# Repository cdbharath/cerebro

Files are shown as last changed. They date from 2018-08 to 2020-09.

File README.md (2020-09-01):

## Cerebro 

A 4-DOF arm that can be controlled using Motor Imagery EEG signals and a haptic feed back system is implemented to materialize the exerted pressure.

The project proposes an approach towards EEG-driven position control of a robot arm by utilizing motor imagery, P300 waveform and Visually evoked Potential to align the robot arm with desired target position. The user produces motor imagery signals to control the motion of the arm. The P300 waveforms gives us sufficient data to detect whether we are performing any motion or even imagining doing so. This becomes even more accurate with C3, C4, PZ, FZ signals coming into picture. Taking these signals as features gives us appropriate information on the motion imagined by the user. This information can be used to control different parameters that are necessary for controlling the arm.

#### Progress:

##### Arm

1. Inverse kinematics equations
After doing a literature survey,the following paper was chosen for developing the inverse kinematics equation for the 4-DOF arm.
https://ieeexplore.ieee.org/document/7166008

2. Simulation in processing

A hand model was developed using Processing. The inverse kinematics equations were solved and the angle was fed to the model to validate the equations.

<p align="center">
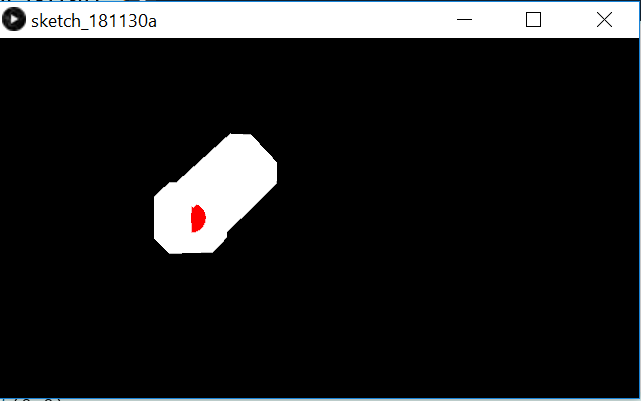
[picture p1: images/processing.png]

</p>

3. Simulation in Gazebo

The arm is simulated in gazebo and rviz by using the CADs designed by us as meshes. The actuation of the joints were controlled by changing the servo angles and the respective output is checked in the simulation.

<p align="center">
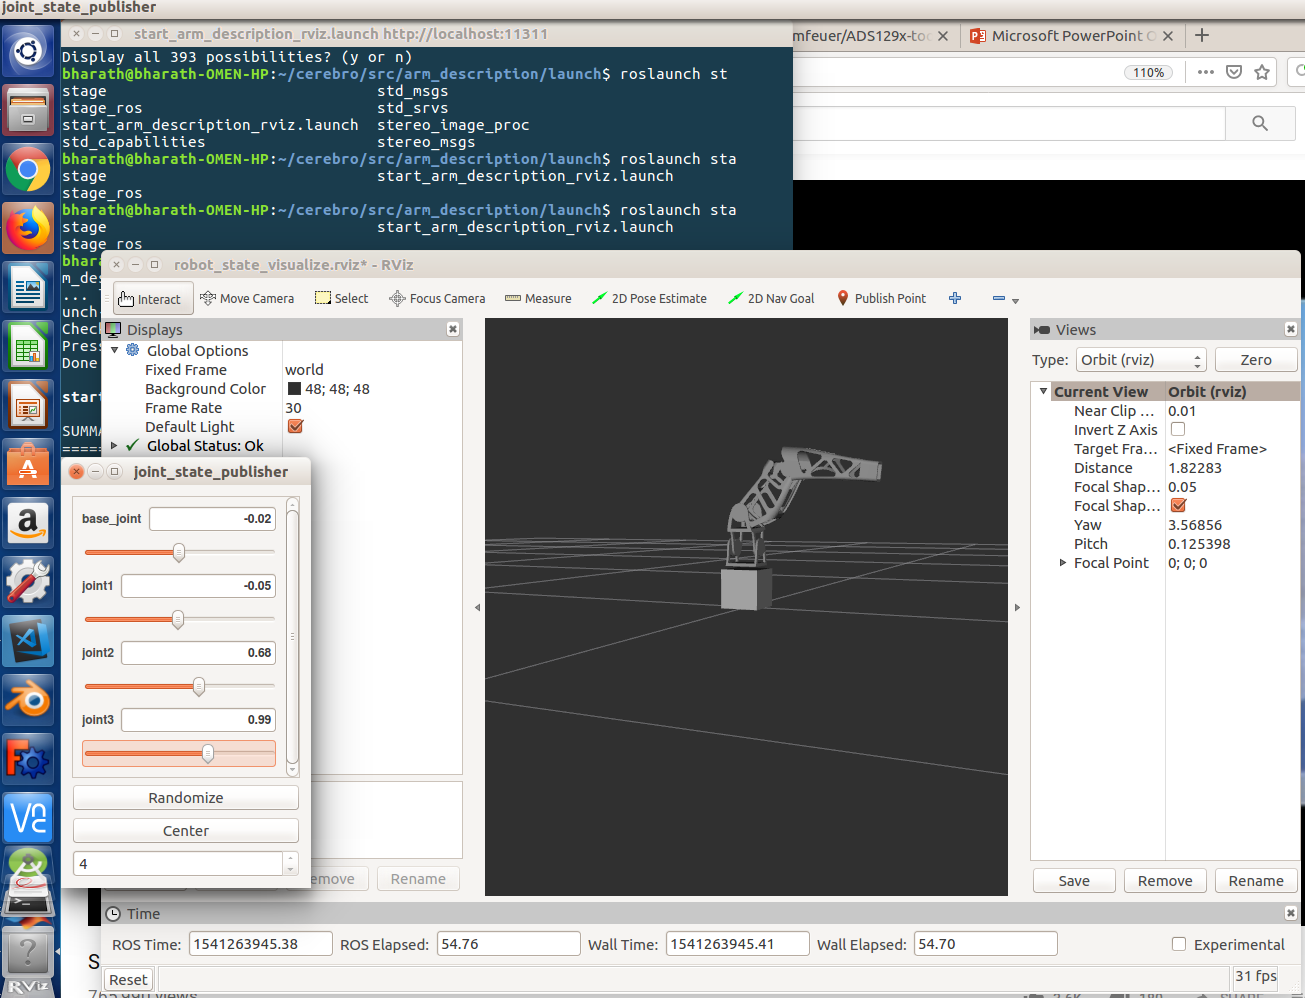
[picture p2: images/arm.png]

</p>

4. Assembly of hand with string mechanisms

The arm parts were assembled with two degrees of freedom in the base joint and one degree of freedom in the elbow joint with the hand attached to the end of the forearm link acting as an end effector. The CAD model of a hand, which had its finger controlled using the string mechanism was obtained from the InMoov website. This model was given for 3d printing. The 3d printed parts were assembled along with the strings. To facilitate the movement of the fingers of robotic arm, the string mechanism was researched upon and found suitable.  This mechanism uses the constancy of the length of wire passing through the finger structure to acquire the desired movement of finger. As the constancy of length was involved, we needed wires which are non stretchable over time and use. Hence we chose fishing braid as the wire that runs through the fingers of our robotic hand. This mechanism required 2 fishing braid wires to run through a single finger and the length of the wires and hence finger movements were controlled using servo motor rotation.

<p align="center">
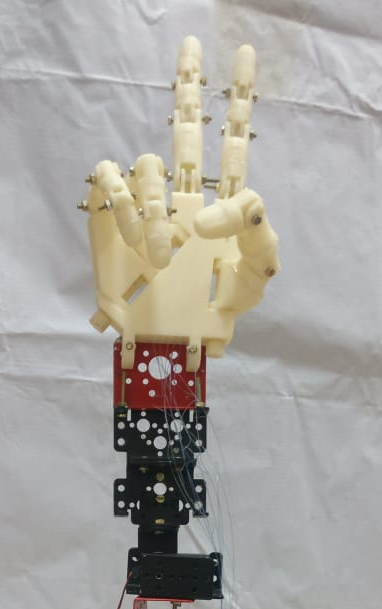
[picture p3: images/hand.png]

</p>

##### Signal Acquisition

1. Tina simulation of the circuit

Second order butterworth filter along with passive high pass filter was designed for the range of 5-20Hz for noise removal from the EEG. The output was then given to an instrumentation amplifier. This circuit was simulated in Tina before trying it out in Breadboard.

<p align="center">
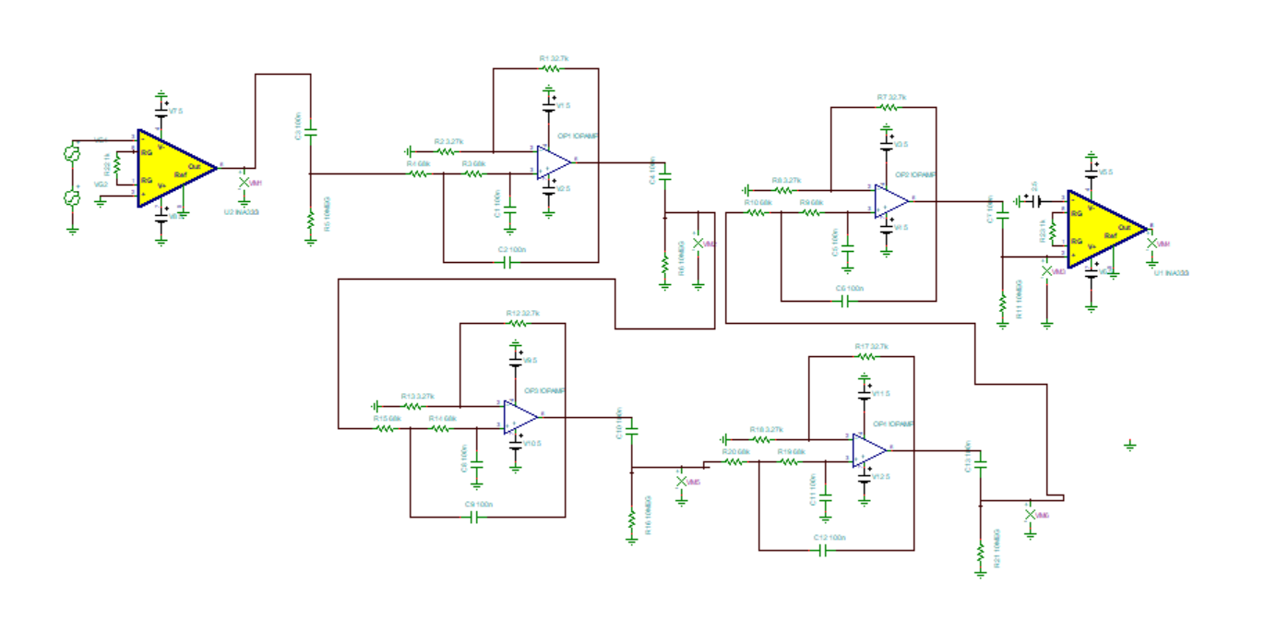
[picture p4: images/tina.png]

</p>

2. Breadboard implementation

The above circuit was practically implemented in the bread board and was validated.

3. PCB design

The same circuit was designed to make a PCB using Proteus software and printed for one channel.

<p align="center">
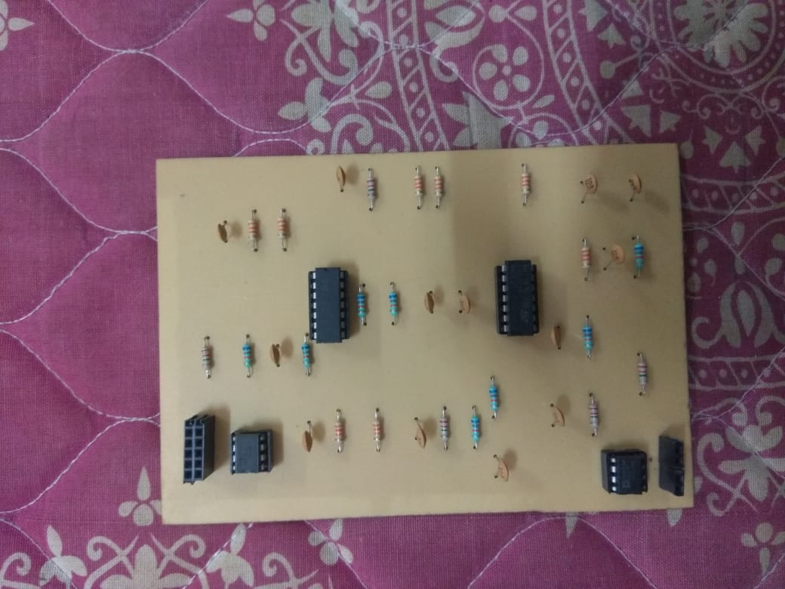
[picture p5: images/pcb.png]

</p>

4. EEG acquisition with OpenBCI Board	

As the designed board was for one channel, and for our application we need four channel, Open BCI board was used.
Due to the high impedance of the electrodes used and the absence of abrasion gel for reducing the impedance due to dead cells, Motor imagery signals were not obtained properly.
Hence EOG signals were acquired and the data was serially communicate to Arduino that checks with threshold and gives the appropriate output.Open BCI GUI was used to program the board on air.

<p align="center">
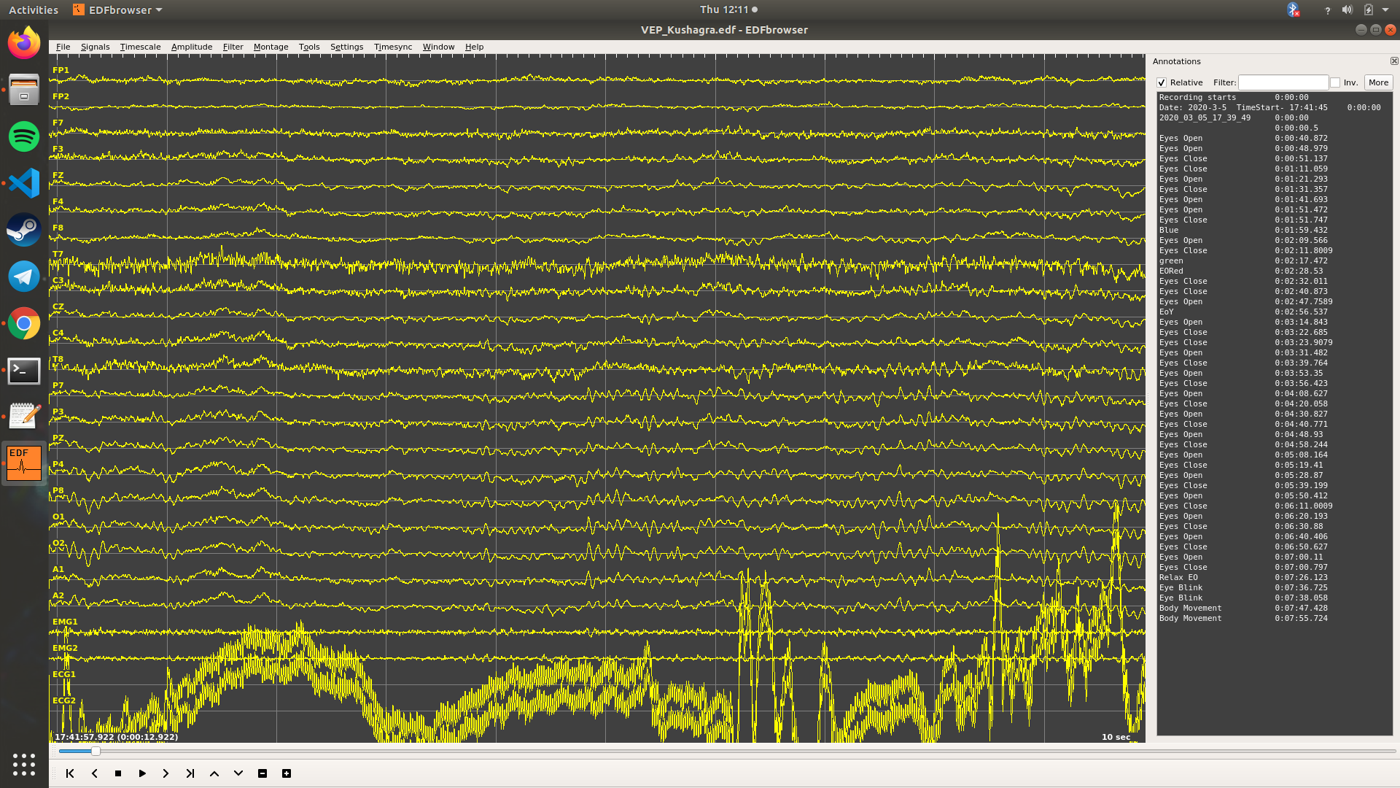
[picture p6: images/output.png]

</p>

##### Haptic feedback

1. Force sensors and Flex sensors
Ideated on interfacing force sensors and flex sensors on the robotic hand. Force sensors are used to measure the force experienced by the robotic arm and have necessary feedback through the pressure actuator in the user’s glove. Flex sensors are used to measure the movements of the finger and the position, which would be used as feedback signal for the positioning of finger. Force sensors and flex sensors were tested and their response to different forces and positioning were recorded.

2. Compressor

Compressor was tested with PWM to give out variable pressure that is necessary for filling the diaphragm. This will make sure that the required force is felt by the wearer of the glove, when the force sensors picks up the sensor values. 

3. Mould CAD design

The mould is a 1.8cm x 1cm x 0.4cm cuboid, designed in CAD and  3D printed. This is the Master mould which will be used for making the base of the balloon actuation mechanism that will will be attached to the fingers of the user.
        
4. Testing 1 (Mould)

One trial of making the PDMS mould was conducted. The curing agent an PDMS were added in the ratio of 1:10 and mixed using stirrer for 5 minutes after which the mixture was degassed in vacuum chamber. This mixture was then transferred to the mould and cured in hot air oven at 80 degrees for 6 hours.  The test did not yield the desired results, a s the PDMS had not solidified and instead had leaked outside the mould. The reason for it i that the terminal groups of the PDMS except hydroxyl and vinyl do not solidify, which I came to know later after analysing the reason for failure.

##### Signal Classification
 
1. CNN algorithm

A convolutional neural net is used to classify the signals     acquired from all the electrodes and classified for jaw clenching and blinking with decent accuracy.

2. Acquired Dataset

EOG data was acquired from electrodes placed on the forehead. Differential outputs from 4 electrodes were taken with respect to ground and used as features for training the model.

3. EOG signals

The EOG signals of 3 different people were obtained for different eye movements. The differences were clearly observable, though the range of values varied time to time and person to person. Therefore calibration and thresholding of the EOG signal was performed in python. The algorithm classifies the movement of eye to top/bottom/right/left.

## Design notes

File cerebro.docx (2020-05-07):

Work done:

Arm

  - Inverse kinematics equations

After doing a literature survey,the following paper was chosen for developing the inverse kinematics equation for the 4-DOF arm.

https://ieeexplore.ieee.org/document/7166008

  - Simulation in processing

A hand model was developed using Processing. The inverse kinematics equations were solved and the angle was fed to the model to validate the equations.


Link: https://github.com/bharath7kumar/Cerebro/blob/master/Hand_Model.pde

- Simulation

The arm is simulated in gazebo and rviz by using the CADs designed by us as meshes. The actuation of the joints were controlled by changing the servo angles and the respective output is checked in the simulation.

Link: https://github.com/bharath7kumar/Cerebro/tree/master/arm_description


  - Plywood arm assembly

An arm assembly using plywoods was tried by us. That didn’t prove to be efficient, and the metal gear servo motors couldn’t hold up the weight with its torque. This was tried to check the inverse kinematics equation.

  - Assembly using e-yantra arm

The arm parts were assembled with two degrees of freedom in the base joint and one degree of freedom in the elbow joint with the hand attached to the end of the forearm link acting as an end effector.

Finger Actuation

  - String mechanism ideation

To facilitate the movement of the fingers of robotic arm, the string mechanism was researched upon and found suitable. This mechanism uses the constancy of the length of wire passing through the finger structure to acquire the desired movement of finger. As the constancy of length was involved, we needed wires which are non stretchable over time and use. Hence we chose fishing braid as the wire that runs through the fingers of our robotic hand. This mechanism required 2 fishing braid wires to run through a single finger and the length of the wires and hence finger movements were controlled using servo motor rotation.

  - 3d printing of finger CADs

The CAD model of a hand, which had its finger controlled using the string mechanism was obtained from the InMoov website. This model was given for 3d printing.

  - Assembly of hand with string mechanisms

The 3d printed parts were assembled along with the strings. One servo motor for each finger was connected to control the actuation of the same. These servo motors were controlled using arduino uno and the desired finger actuation was observed.

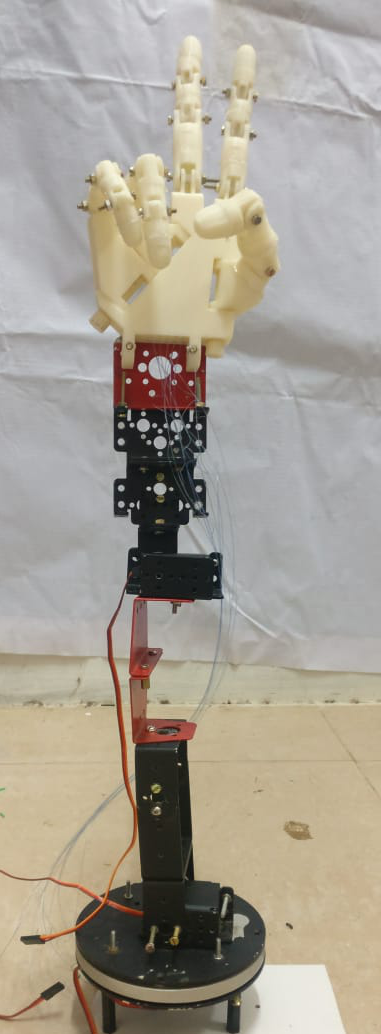
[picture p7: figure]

Signal Acquisition

  - Ads1299 Evaluation Board

Acquisition of signals using TI’s ADS1299 Evaluation board was tried. The SPI communication failed which may be due to the failure of board.Interface was first tried, using the ADS1299 GUI which the TI provided specially for this Evaluation board.

Secondly, Interface was done using SPI communication between the Arduino and the Evaluation board.

Hardware components used along with the board were checked to conclude that the board is at fault.

  - Tina simulation of the circuit

Second order butterworth filter along with passive high pass filter was designed for the range of 5-20Hz for noise removal from the EEG. The output was then given to an instrumentation amplifier. This circuit was simulated in Tina before trying it out in Breadboard.


  - Breadboard implementation

The above circuit was practically implemented in the bread board and was validated.

  - PCB design

The same circuit was designed to make a PCB using Proteus software and printed for one channel.


  - OpenBCI board

As the designed board was for one channel, and for our application we need four channel, Open BCI board was used.

Due to the high impedance of the electrodes used and the absence of abrasion gel for reducing the impedance due to dead cells, Motor imagery signals were not obtained properly.

Hence EOG signals were acquired and the data was serially communicate to Arduino that checks with threshold and gives the appropriate output.Open BCI GUI was used to program the board on air.

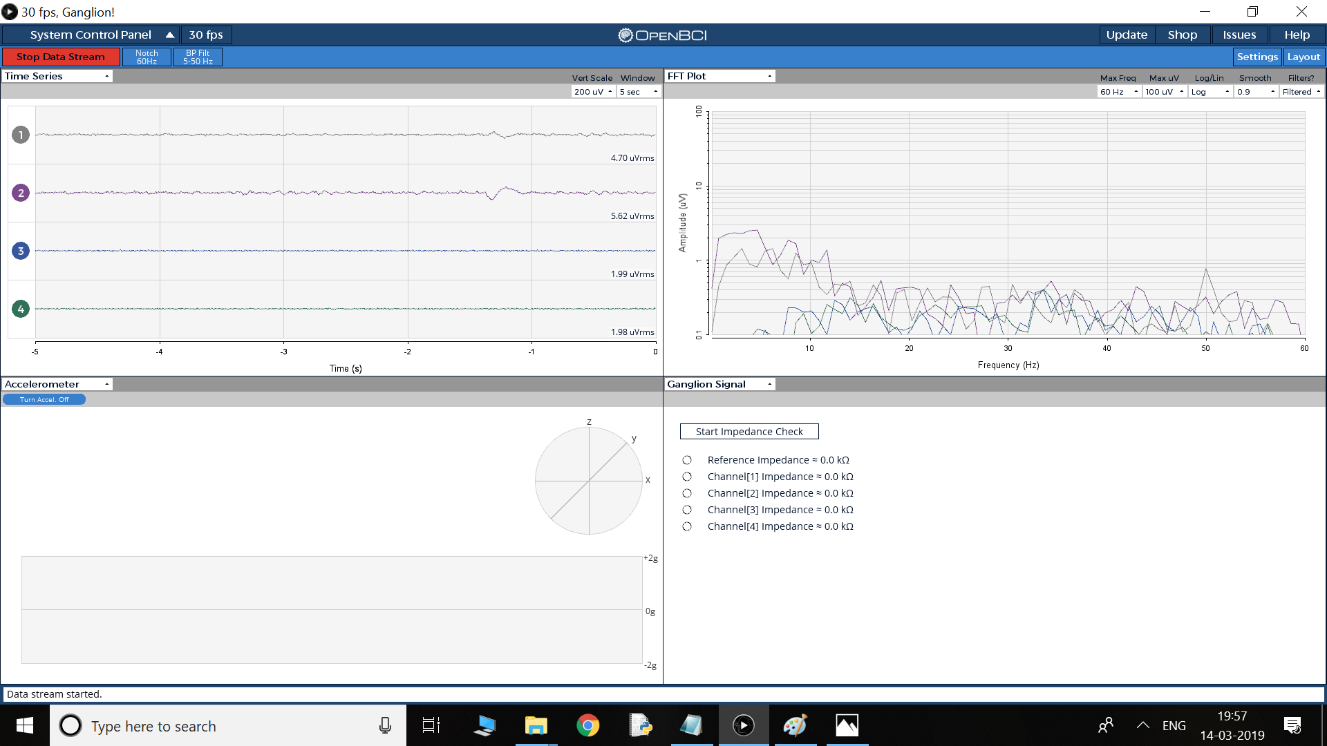
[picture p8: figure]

Haptic feedback

  - Force sensors and Flex sensors

Ideated on interfacing force sensors and flex sensors on the robotic hand. Force sensors are used to measure the force experienced by the robotic arm and have necessary feedback through the pressure actuator in the user’s glove. Flex sensors are used to measure the movements of the finger and the position, which would be used as feedback signal for the positioning of finger. Force sensors and flex sensors were tested and their response to different forces and positioning were recorded.

  - Compressor

Compressor was tested with PWM to give out variable pressure that is necessary for filling the diaphragm. This will make sure that the required force is felt by the wearer of the glove, when the force sensors picks up the sensor values.

  - Mould CAD design

The mould is a 1.8cm x 1cm x 0.4cm cuboid, designed in CAD

and 3D printed. This is the Master mould which will be used

for making the base of the balloon actuation mechanism that will

will be attached to the fingers of the user.

  - Testing 1 (Mould)

One trial of making the PDMS mould was conducted. The curing agent an PDMS were added in the ratio of 1:10 and mixed using stirrer for 5 minutes after which the mixture was degassed in vacuum chamber. This mixture was then transferred to the mould and cured in hot air oven at 80 degrees for 6 hours. The test did not yield the desired results, a s the PDMS had not solidified and instead had leaked outside the mould. The reason for it i that the terminal groups of the PDMS except hydroxyl and vinyl do not solidify, which I came to know later after analysing the reason for failure.

Signal Classification

  - CNN algorithm

A convolutional neural net is used to classify the signals acquired from all the electrodes and classified for jaw clenching and blinking with decent accuracy.

  - Acquired Dataset

EOG data was acquired from electrodes placed on the forehead. Differential outputs from 4 electrodes were taken with respect to ground and used as features for training the model.

Link: https://github.com/bharath7kumar/Cerebro/tree/master/data

  - EOG signals

The EOG signals of 3 different people were obtained for different eye movements. The differences were clearly observable, though the range of values varied time to time and person to person. Therefore calibration and thresholding of the EOG signal was performed in python. The algorithm classifies the movement of eye to top/bottom/right/left.

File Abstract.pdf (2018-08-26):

# Cerebro

Motor Imagery based Prosthetic arm control with Haptic feedback

Bharath, Amritha, Aradhana, Bhavya, Rakesh, Pooja, Veejay

Abstract

A 6-DOF arm that can be controlled using Motor Imagery EEG signals and a haptic feed back system is implemented to materialize the exerted pressure.

## 1 Introduction

The project proposes an approach towards EEG-driven position control of a robot arm by utilizing motor imagery, P300 waveform and Visually evoked Potential to align the robot arm with desired target position.
The user produces motor imagery signals to control the motion of the arm. The P300 waveforms gives us sufficient data to detect whether we are performing any motion or even imagining doing so. This becomes even more accurate with C3, C4, PZ, FZ signals coming into picture. Taking these signals as features gives us appropriate information on the motion imagined by the user. This information can be used to control different parameters that are necessary for controlling the arm.
This Project has a lot of Applications. This will facilitate the living of individuals with upper extremity impairment. The Brain-computer interface can act as a medium for them to use robotic arm for the activities of their daily life. Haptic feedback will give them the sense of touch. This can be achieved by giving neuro-feed back to the brain. The haptic feedback can be very helpful when it comes to invasive surgery using robotic arms.

## 2 Methodology

### 2.1 Building a 6DOF arm

A 6DOF humanoid arm is built by 3d printing the CAD model open sourced by Poppy Project, a humanoid robotic startup. The final arm will be capable of traversing any x,y,z coordinates within the range, along with rolling, rotating of the arm. Six servos are attached on the elbow, wrist and shoulder, each two respectively. Extra servos will be needed for the finger movements. The movement of the arm is achieved with inverse kinematics.

1

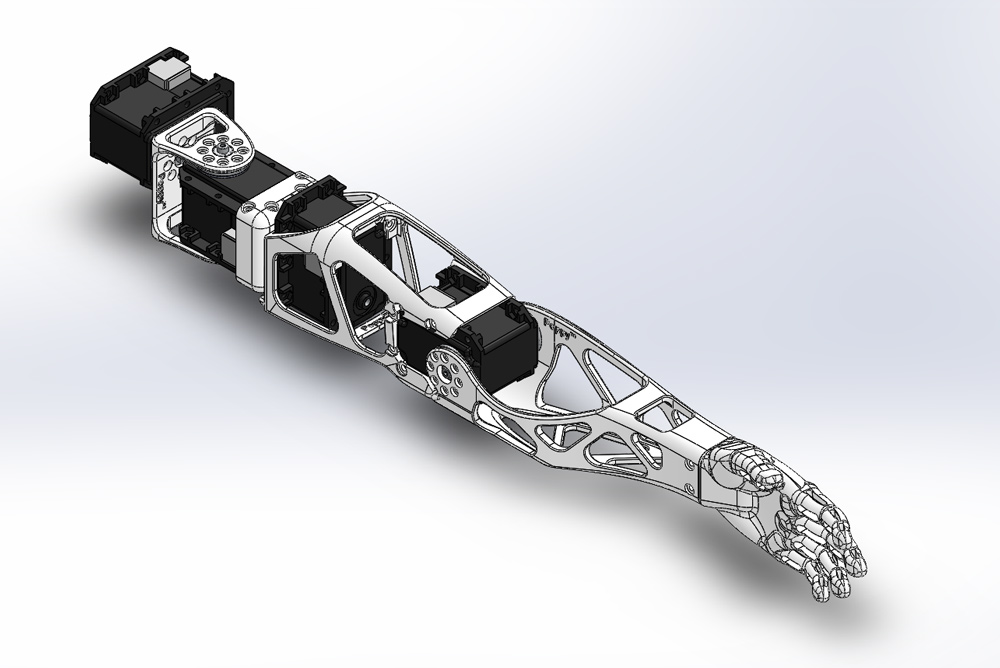
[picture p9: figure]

Figure 1: The CAD model.

### 2.2 Inverse Kinematics

Inverse kinematics problem of a robot is finding the angles of the robot by having the end position. It allows us to traverse our gripper to specific coordinate mentioned and grab a particular object. Higher degrees of freedom will have a more complicated solution. The length of each edge is considered to get the final joint angles.

### 2.3 Control with Flex sensors

The flex sensor uses flexible conductive ink printed on flexible base forming a resistor. It works when bent with the ink on the outside of the curve. When bent, the outside layer is stretched and thus extends, resulting in reduced cross section. This reduced cross section and increased length results in an increased resistance, which can be measured.
This variable resistance of the flex sensor can be mapped to different positions of the finger. Different fingers of the robotic arm will have different flex sensors attached to it. The position of each finger, calculated from the EEG Signal, will be the required value. The flex sensors’ resistance will give us actual positions of the fingers. A suitable linear control algorithm will be framed to bring the actual position close to or exactly same as the calculated position using servo motors.
The resistance of the flex sensor can be obtained by combining the flex sensor with a static resistor to create a voltage divider, which can produce a variable voltage that can be read by analog-to-digital converter of a micro controller.

### 2.4 Haptic feedback

Force sensors are placed at the fingers of the robotic arm. The data is serially transmitted to the controller.Glove has PDMS membrane embedded in it. PDMS is viscoelastic material.Balloon actuation is achieved by the pressure dependent swelling and saturation phenomena of 2 flexible PDMS diaphragms.Top

2

diaphragm layer has horizontal channels where the air can be pumped from an external compressor which is controlled using PWM in accordance with the data obtained from force sensor.

### 2.5 Electrode Placements

The signals we will be needing for motor imagery are C3, C4, PZ, FZ region. These regions are present in the central region of our head. EEG electrodes are placed in the respective positions along with the reference electrode which is placed over any of the ear lobe. The reference electrode is given as The reference electrode is given to shorted negative terminals of the channels, while the other four electrodes are given to positive terminal of the respective channels.

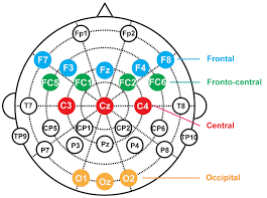
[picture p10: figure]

Figure 2: Electrode placement.

### 2.6 EEG signal Acquisition

ADS1299 is a device by Texas Instruments. It has 8 channels, that is, 8 differential amplifiers. The negative terminal of the amplifiers can be shorted and reference voltage is applied, which will be the same across all negative terminals. The common mode noise is significantly reduced on giving input signals through the differential amplifier. The dc noise is reduced by adding a High pass filter with sufficient cutoff voltage. The 50hz live-line voltage interference can be reduced in a similar way by adding a low pass filter with a cutoff frequency of 40hz. A better way to reduce 50hz noise is to implement second order butter worth filter ,the roll off doubles up reducing the noise even more.
The output signal from ADS1299 is sent to Arduino using serial Peripheral interface.This is further transferred to PC serially. Python receives the serial data and feeds the data to classification algorithm.

3

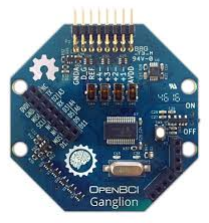
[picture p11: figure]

Figure 3: The acquisition board.

### 2.7 Motor Imagery Data Classification

The data is saved in a data buffer of length 5 seconds. The number of samples will be the baudrate * 5. This data is fed either to SVM Classifier or CNN or RNN. The model is chosen based on the validation accuracy. SVM is currently the popular algorithm used for EEG signal classification. The classic, one vs rest classification can be used to classify the signals from one another. But using Recurrent Neural Networks may improve the accuracy significantly since EEG signal is a time series. The data is fed into Recurrent neural networks with applicable hyper parameters to get the final output.

### 2.8 Control using Classification output

We have to control the up/down, right/left, top/bottom, yaw, pitch, roll of the arm. Since the only varying parameters in the inverse kinematics equation of 6dof arm are X, Y, Z coordinates, roll, pitch, yaw, we can easily control the arm using few parameters. An additional parameter is needed for the grasping of fists. The output from the classification algorithm can be used to control these parameters thereby controlling the arm. The two step process includes moving the arm in the horizontal plane right above the target object. The moving the arm vertically down until we reach the object. Then we use the grasp parameter to grab the object and again use the two step process to place the object somewhere else. The two step process is preferred because it requires comparatively lesser parameters and is easier to control.

## 3 Further Improvements

The Arm control can be further improved with visual feedback. The video camera may be placed in back of the hand or we can use the aerial view. Then

4

we can use the error in visual feed back for better control. Reinforcement learning algorithm can be used to train the arm from its mistakes. The model will allow the arm to overcome its previous mistakes, finally ending up doing the required action.

## 4 Requirements

### 4.1 Hardware Requirements

1. Acquisition device
2. 3d Printed STLs
3. EEG electrodes
4. Electrode paste
5. Servo Motors
6. Flex sensors
7. Air Pump
8. Rubber Gloves
9. Vibration sensors

### 4.2 Software Requirements

1. Python
2. ROS
3. Tensorflow or Pytorch
4. Arduino IDE

## 5 References

- Saugat Bhattacharyya, Amit KonarD, N. Tibarewala ”Motor imagery, P300 and error-related EEG-based robot arm movement control for rehabilitation purpose”
- Ming-ai , Meng Zhang , Yan-jun Sun ”A novel motor imagery EEG recognition method based on deep learning”
- Alireza Khatamian ”Solving Kinematics Problems of a 6-DOF Robot Manipulator”
- Poppy Project github repository ”https://github.com/poppy-project/Poppybasic-arms”

5

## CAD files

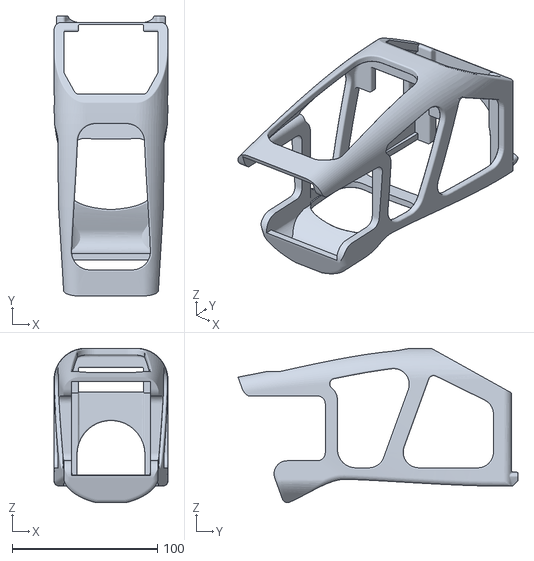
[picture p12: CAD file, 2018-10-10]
CADs/Arm/upper_arm.stl
78.5 x 192.9 x 106.3

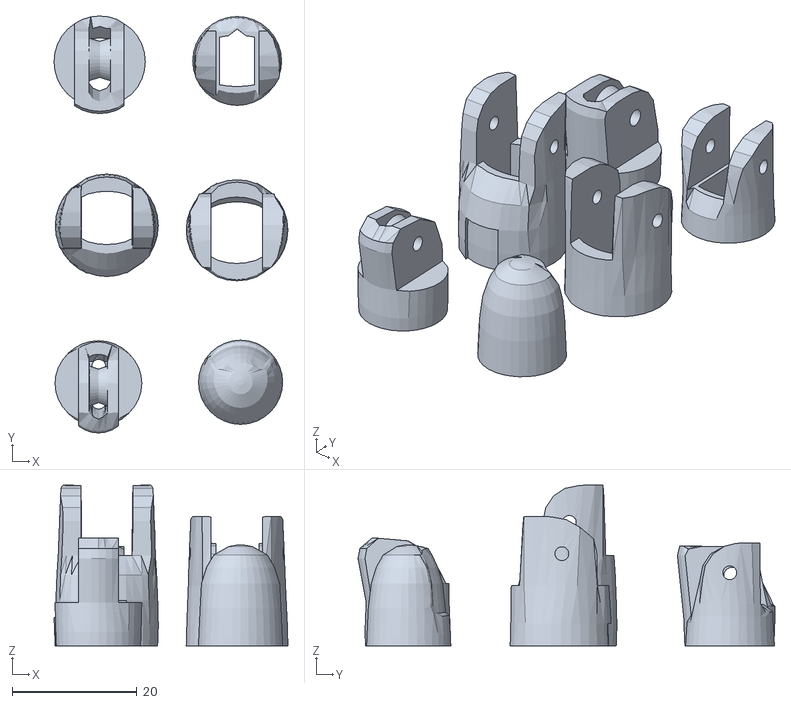
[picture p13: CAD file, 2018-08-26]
CADs/Hand/ringfinger3.stl
37.6 x 67.0 x 25.8

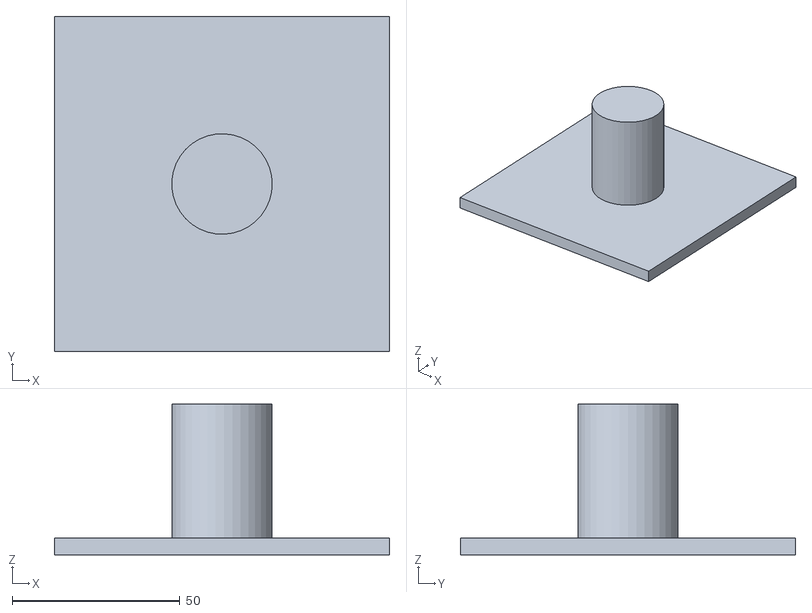
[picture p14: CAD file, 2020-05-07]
Simulation/New_arm/Sample CAD model/arm-cerebro-ross - shoulder-plate-1.STL
100.0 x 100.0 x 45.0

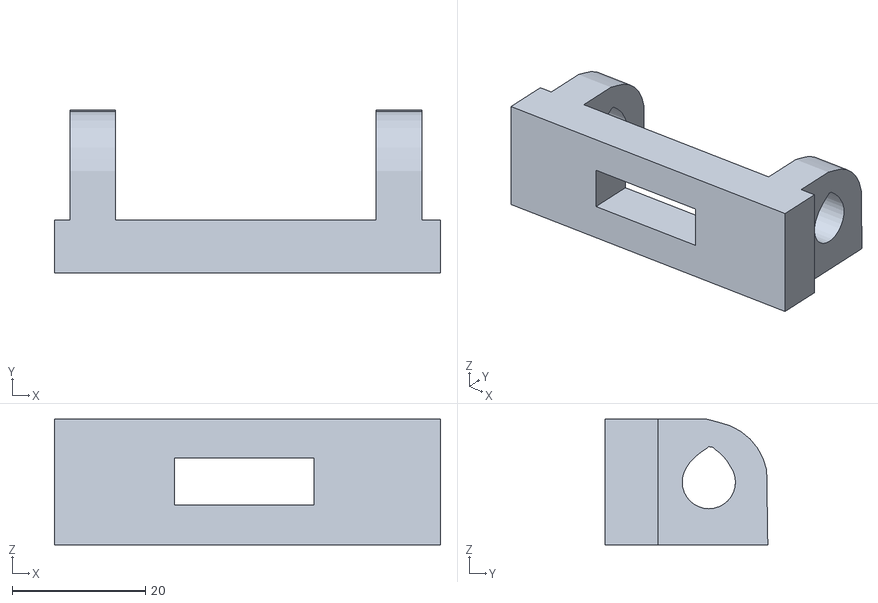
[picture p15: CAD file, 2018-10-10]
CADs/Arm/hand_connector.STL
58.0 x 24.4 x 18.9

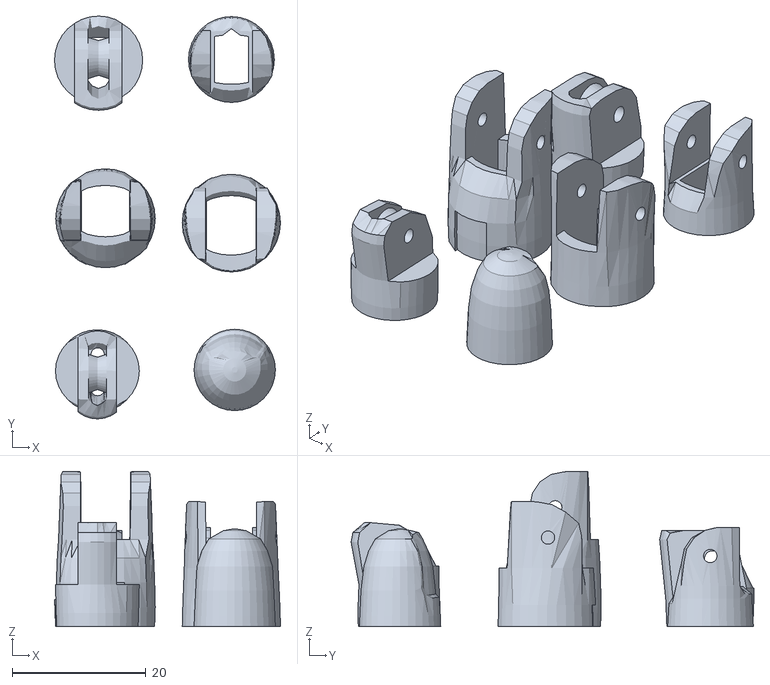
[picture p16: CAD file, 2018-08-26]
CADs/Hand/Auriculaire3.stl
33.8 x 60.3 x 23.2

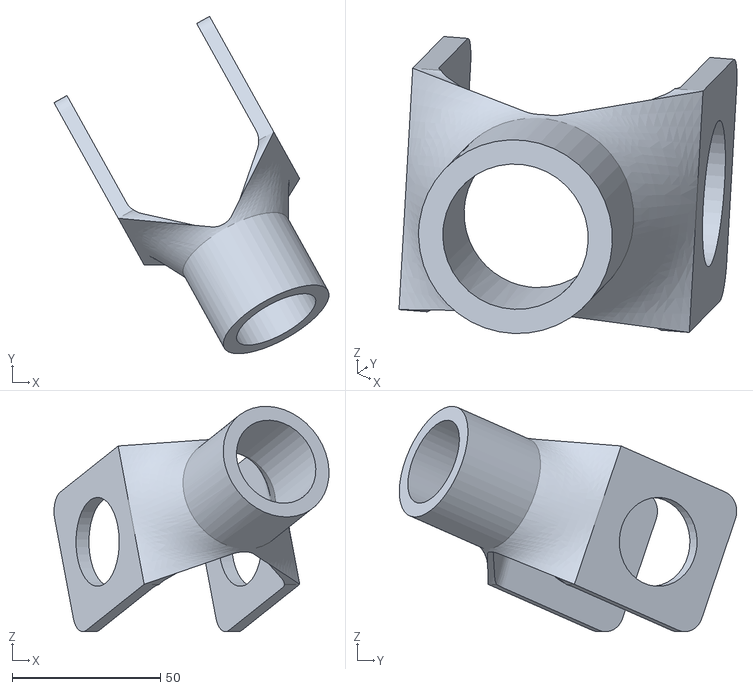
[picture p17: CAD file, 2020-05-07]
Simulation/New_arm/Sample CAD model/arm-cerebro-ross - shoulder-hinge-2.STL
92.7 x 113.8 x 75.9

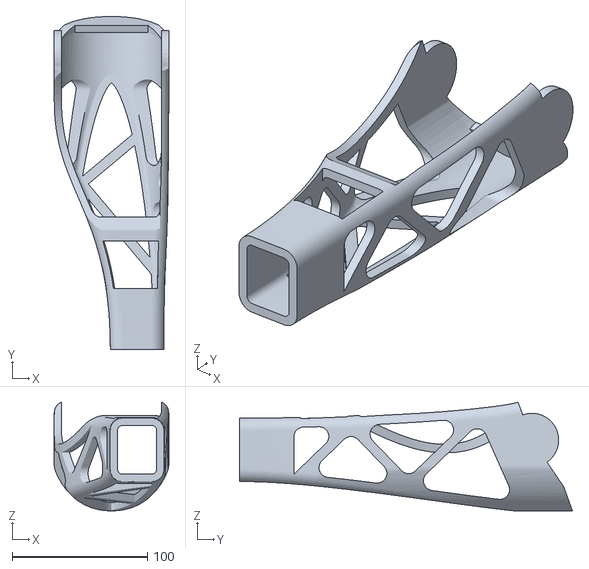
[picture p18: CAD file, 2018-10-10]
CADs/Arm/forearm.STL
84.6 x 246.0 x 80.4

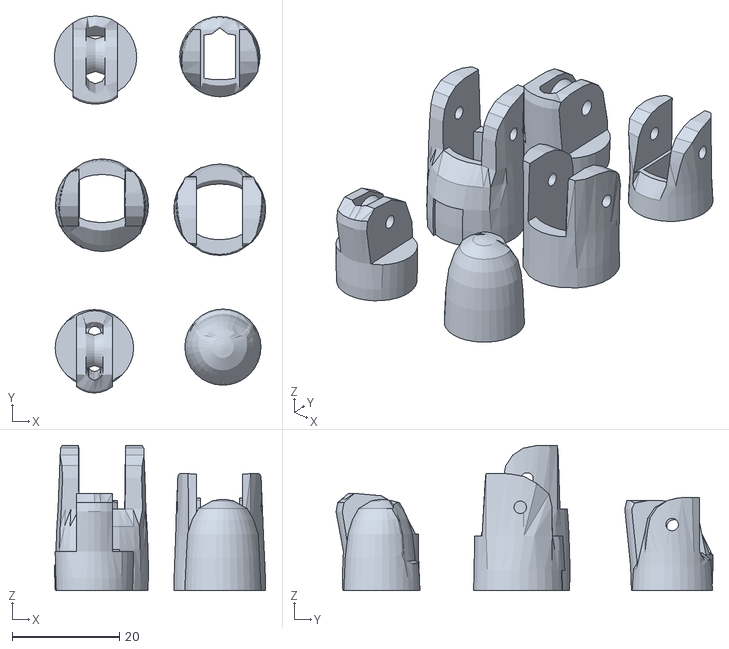
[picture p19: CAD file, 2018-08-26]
CADs/Hand/Index3.stl
39.4 x 70.2 x 27.0

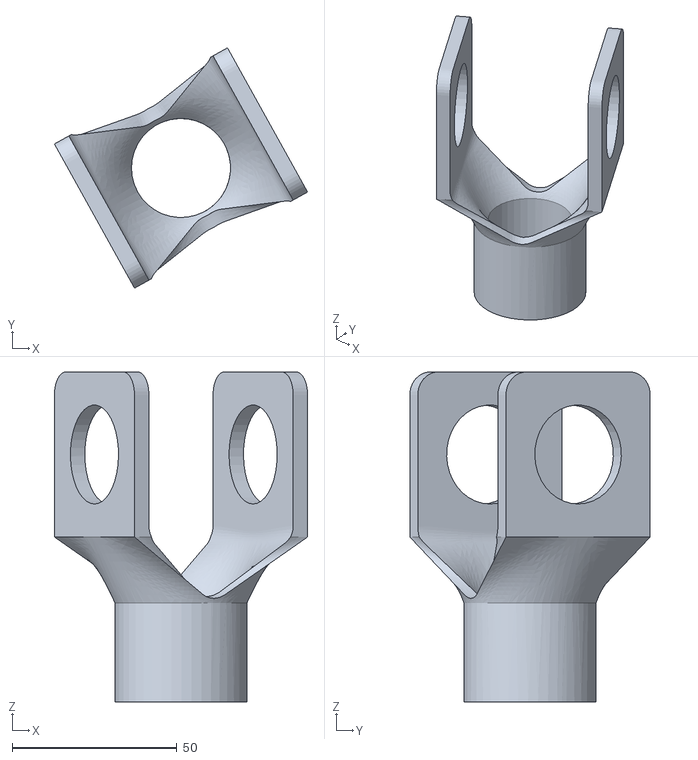
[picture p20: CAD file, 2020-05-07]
Simulation/New_arm/Sample CAD model/arm-cerebro-ross - shoulder-hinge-1.STL
76.7 x 72.8 x 100.0

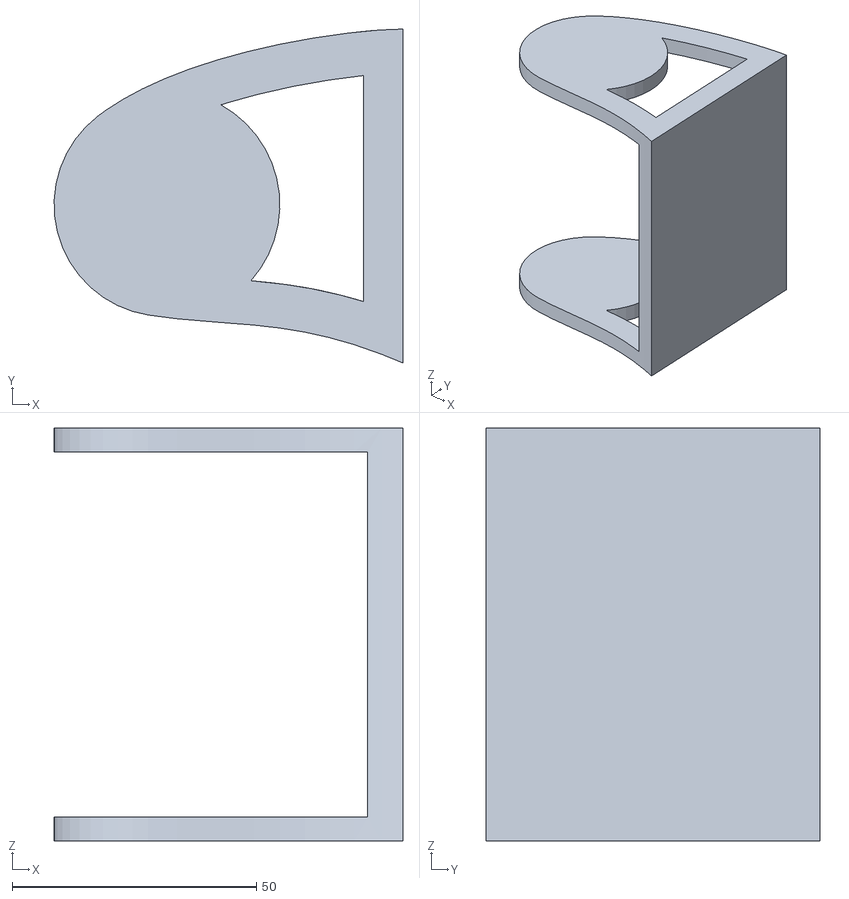
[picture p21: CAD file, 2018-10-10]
CADs/Arm/shoulder_connector_1.STL
71.4 x 68.4 x 84.6

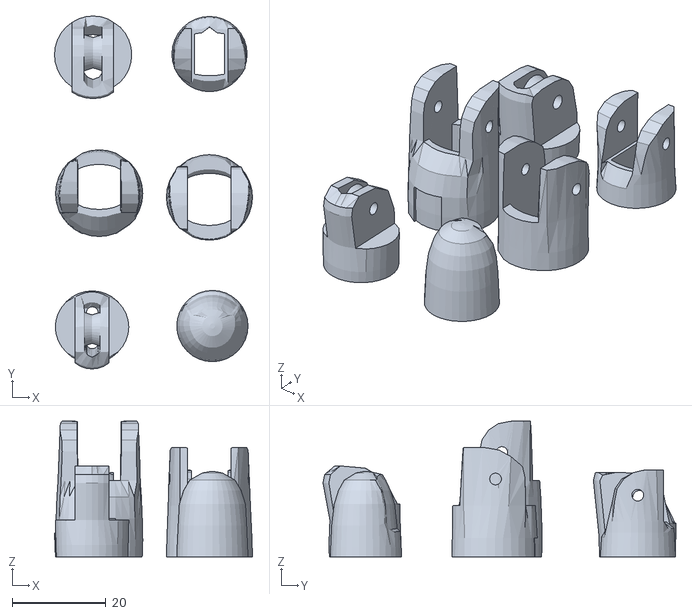
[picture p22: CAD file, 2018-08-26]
CADs/Hand/Majeure3.stl
42.2 x 75.2 x 29.0

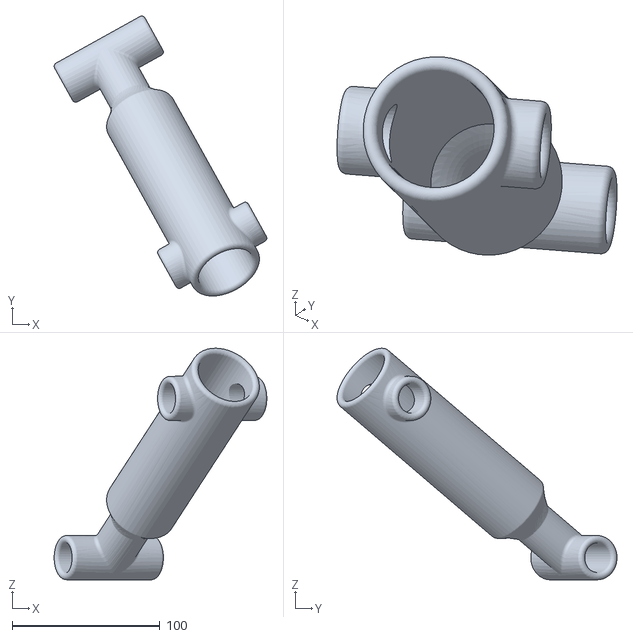
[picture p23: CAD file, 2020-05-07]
Simulation/New_arm/Sample CAD model/arm-cerebro-ross - arm-1.STL
143.9 x 189.5 x 156.8

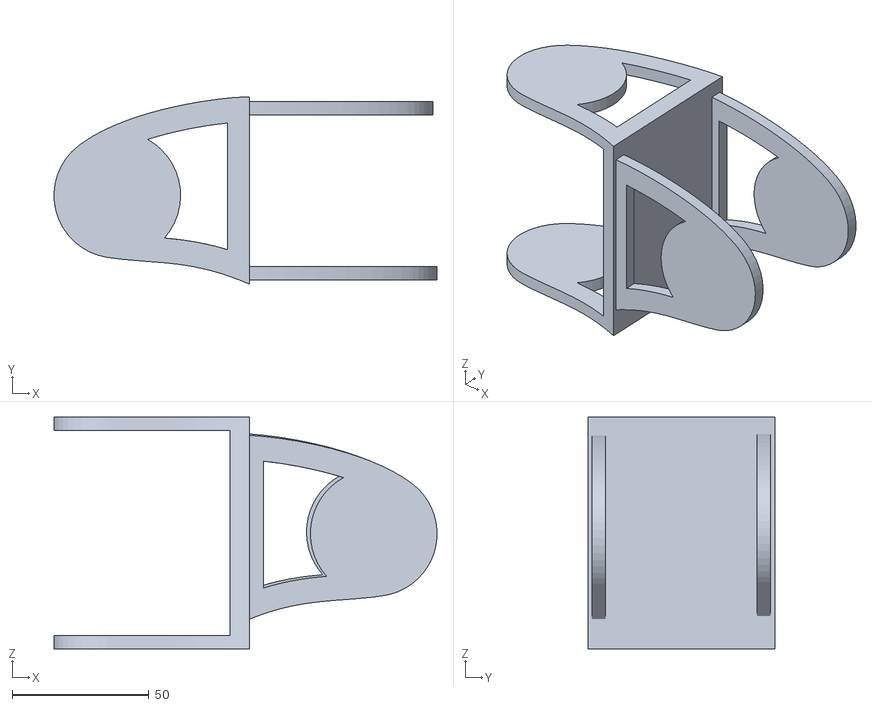
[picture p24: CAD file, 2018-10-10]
CADs/Arm/shoulder_connector_2.STL
139.8 x 68.4 x 84.6

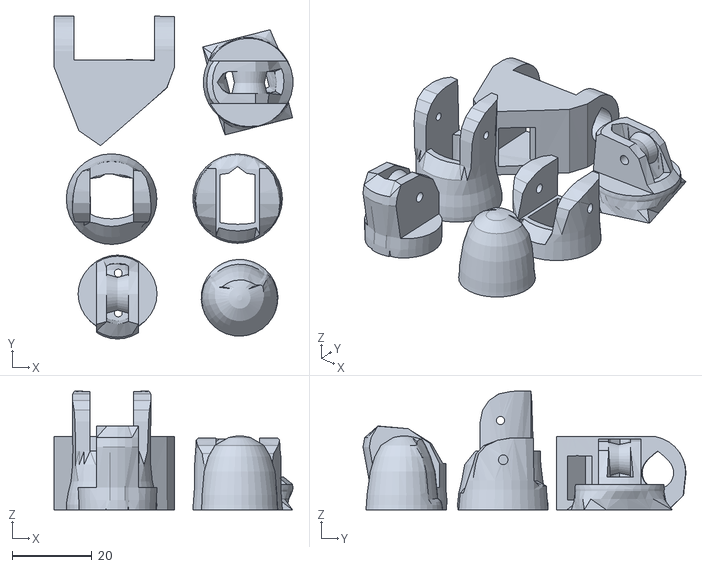
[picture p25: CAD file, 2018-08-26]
CADs/Hand/thumb5.stl
60.1 x 81.2 x 29.8

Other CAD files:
CADs/Hand/WristlargeV4.stl
CADs/Hand/WristsmallV4.stl
CADs/Hand/Bolt_entretoise7.stl

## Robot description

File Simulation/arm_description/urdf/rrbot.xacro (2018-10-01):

<?xml version="1.0"?>
<!-- Revolute-Revolute Manipulator -->
<robot name="rrbot" xmlns:xacro="http://www.ros.org/wiki/xacro">

  <!-- Constants for robot dimensions -->
  <xacro:property name="PI" value="3.1415926535897931"/>
  <xacro:property name="mass" value="1" /> <!-- arbitrary value for mass -->
  <xacro:property name="width" value="0.1" /> <!-- Square dimensions (widthxwidth) of beams -->
  <xacro:property name="height1" value="2" /> <!-- Link 1 -->
  <xacro:property name="height2" value="1" /> <!-- Link 2 -->
  <xacro:property name="height3" value="1" /> <!-- Link 3 -->
  <xacro:property name="camera_link" value="0.05" /> <!-- Size of square 'camera' box -->
  <xacro:property name="axel_offset" value="0.05" /> <!-- Space btw top of beam and the each joint -->

  <!-- Import all Gazebo-customization elements, including Gazebo colors -->
  <xacro:include filename="$(find rrbot_description)/urdf/rrbot.gazebo" />
  <!-- Import Rviz colors -->
  <xacro:include filename="$(find rrbot_description)/urdf/materials.xacro" />

  <!-- Used for fixing robot to Gazebo 'base_link' -->
  <link name="world"/>

  <joint name="fixed" type="fixed">
    <parent link="world"/>
    <child link="base"/>
  </joint>

  <!-- base -->
  <link name="base">
    <collision>
      <origin xyz="0 0 0.05" rpy="0 0 0"/>
      <geometry>
	<box size="0.1 0.1 0.1"/>
      </geometry>
    </collision>

    <visual>
      <origin xyz="0 0 0.05" rpy="0 0 0"/>
      <geometry>
	<box size="0.1 0.1 0.1"/>
      </geometry>
      <material name="orange"/>
    </visual>

    <inertial>
      <origin xyz="0 0 0" rpy="0 0 0"/>
      <mass value="${mass}"/>
      <inertia ixx="${mass / 12.0 * (width*width + height1*height1)}" ixy="0.0" ixz="0.0" iyy="${mass / 12.0 * (height1*height1 + width*width)}" iyz="0.0" izz="${mass / 12.0 * (width*width + width*width)}"/>
    </inertial>
  </link>

  <joint name="base_joint" type="continuous">
    <parent link="base"/>
    <child link="link1"/>
    <origin xyz="0 0 0" rpy="0 0 0"/>
    <axis xyz="0 0 1"/>
    <dynamics damping="0.7"/>
  </joint>

  <!-- link1 -->
  <link name="link1">
    <collision>
      <origin xyz="-0.039 0.042 0.18" rpy="1.57 1.57 0"/>
      <geometry>
	<mesh filename="package://arm_description/meshes/collision/shoulderconnector1.dae" scale="0.001 0.001 0.001"/>
      </geometry>
    </collision>

    <visual>
      <origin xyz="-0.039 0.042 0.18" rpy="1.57 1.57 0"/>
      <geometry>
	<mesh filename="package://arm_description/meshes/visual/shoulderconnector1.dae" scale="0.001 0.001 0.001"/>
      </geometry>
      <material name="orange"/>
    </visual>

    <inertial>
      <origin xyz="0 0 0" rpy="0 0 0"/>
      <mass value="${mass}"/>
      <inertia ixx="${mass / 12.0 * (width*width + height1*height1)}" ixy="0.0" ixz="0.0" iyy="${mass / 12.0 * (height1*height1 + width*width)}" iyz="0.0" izz="${mass / 12.0 * (width*width + width*width)}"/>
    </inertial>
  </link>

  <joint name="joint1" type="continuous">
    <parent link="link1"/>
    <child link="link2"/>
    <origin xyz="0 0 0.18" rpy="0 0 0"/>
    <axis xyz="0 1 0"/>
    <dynamics damping="0.7"/>
  </joint>

  <!-- link2 -->
  <link name="link2">
    <collision>
      <origin xyz="0 0 0.02" rpy="0 1.56 0"/>
      <geometry>
	<mesh filename="package://arm_description/meshes/collision/shoulderconnector2.dae" scale="0.001 0.001 0.001"/>
      </geometry>
    </collision>

    <visual>
      <origin xyz="0 0 0.02" rpy="0 1.56 0"/>
      <geometry>
        <mesh filename="package://arm_description/meshes/visual/shoulderconnector2.dae" scale="0.001 0.001 0.001"/>
      </geometry>
      <material name="orange"/>
    </visual>

    <inertial>
      <origin xyz="0 0 0" rpy="1.56 0 0"/>
      <mass value="${mass}"/>
      <inertia ixx="${mass / 12.0 * (width*width + height2*height2)}" ixy="0.0" ixz="0.0" iyy="${mass / 12.0 * (height2*height2 + width*width)}" iyz="0.0" izz="${mass / 12.0 * (width*width + width*width)}"/>
    </inertial>
  </link>

  <joint name="joint2" type="continuous">
    <parent link="link2"/>
    <child link="link3"/>
    <origin xyz="0 0 0.05" rpy="0 0 0"/>
    <axis xyz="1 0 0"/>
    <dynamics damping="0.7"/>
  </joint>

  <!-- link3 -->
  <link name="link3">
    <collision>
      <origin xyz="0.04 0.04 0.2" rpy="1.57 3.14 0"/>
      <geometry>
	<mesh filename="package://arm_description/meshes/collision/upper_arm.dae" scale="0.001 0.001 0.001"/>
      </geometry>
    </collision>

    <visual>
      <origin xyz="0.04 0.04 0.2" rpy="1.57 3.14 0"/>
      <geometry>
        <mesh filename="package://arm_description/meshes/visual/upper_arm.dae" scale="0.001 0.001 0.001"/>
      </geometry>
      <material name="black"/>
    </visual>

    <inertial>
      <origin xyz="0 0 0" rpy="1.56 0 0"/>
      <mass value="${mass}"/>
      <inertia ixx="${mass / 12.0 * (width*width + height2*height2)}" ixy="0.0" ixz="0.0" iyy="${mass / 12.0 * (height2*height2 + width*width)}" iyz="0.0" izz="${mass / 12.0 * (width*width + width*width)}"/>
    </inertial>
  </link>
  
  <joint name="joint3" type="continuous">
    <parent link="link3"/>
    <child link="link4"/>
    <origin xyz="0 0 0.18" rpy="0 0 0"/>
    <axis xyz="1 0 0"/>
    <dynamics damping="0.7"/>
  </joint>

  <!-- link4 -->
  <link name="link4">
    <collision>
      <origin xyz="0.04 0.035 0.24" rpy="-1.57 0 3.14"/>
      <geometry>
	<mesh filename="package://arm_description/meshes/collision/forearm.dae" scale="0.001 0.001 0.001"/>
      </geometry>
    </collision>

    <visual>
      <origin xyz="0.04 0.035 0.24" rpy="-1.57 0 3.14"/>
      <geometry>
        <mesh filename="package://arm_description/meshes/visual/forearm.dae" scale="0.001 0.001 0.001"/>
      </geometry>
      <material name="black"/>
    </visual>

    <inertial>
      <origin xyz="0 0 0" rpy="1.56 0 0"/>
      <mass value="${mass}"/>
      <inertia ixx="${mass / 12.0 * (width*width + height2*height2)}" ixy="0.0" ixz="0.0" iyy="${mass / 12.0 * (height2*height2 + width*width)}" iyz="0.0" izz="${mass / 12.0 * (width*width + width*width)}"/>
    </inertial>
  </link>

</robot>

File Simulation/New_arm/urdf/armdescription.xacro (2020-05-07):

<?xml version="1.0" ?>

<robot name="basicarm" xmlns:xacro="http://www.ros.org/wiki/xacro">
    <link name="base_link">
        <visual>
            <origin rpy="0 0 0" xyz="0 0 0"/>
            <geometry>
                <cylinder radius="0.5" length="1"/>
            </geometry>
        </visual>
    </link>
    
    <joint name="base_link__link_01" type="revolute">
        <axis xyz="0 0 1" />
        <limit effort="1000.0" lower="-3.14" upper="3.14" velocity="0.5"/>
        <origin py="0 0 0" xyz="0 0 0.5"/>
        <parent link="base_link"/>
        <child link="link1"/>
    </joint>
    
    <link name="link1">
        <visual>
            <origin rpy="0 0 0" xyz="0 0 0"/>
            <geometry>
                <cylinder radius="0.35" length="0.2"/>
            </geometry>
        </visual>
    </link>

    <joint name="link1__link_2" type="revolute">
        <axis xyz="0 1 0" />
        <limit effort="1000.0" lower="-3.14" upper="3.14" velocity="0.5"/>
        <origin py="0 0 0" xyz="0 0 0.7"/>
        <parent link="link1"/>
        <child link="link2"/>
    </joint>


    <link name="link2">
        <visual>
            <origin rpy="0 0 0" xyz="0 0 0"/>
            <geometry>
                <cylinder radius="0.2" length="1.0"/>
            </geometry>
        </visual>
    </link>

    <joint name="link2__link_3" type="revolute">
        <axis xyz="0 1 0" />
        <limit effort="1000.0" lower="-3.14" upper="3.14" velocity="0.5"/>
        <origin py="0 0 0" xyz="0 0 1.35"/>
        <parent link="link2"/>
        <child link="link3"/>
    </joint>


    <link name="link3">
        <visual>
            <origin rpy="0 0 0" xyz="0 0 0"/>
            <geometry>
                <cylinder radius="0.2" length="1.0"/>
            </geometry>
        </visual>
    </link>



</robot>

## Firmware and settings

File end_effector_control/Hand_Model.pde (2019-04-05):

float x, y,x1,y1,z1,r=100;
float angle1 = 0.0;
float angle2 = 0.0;
float angle3=0.0;
float angle4=0.0;
float segLength = 100;
float d=0,e=0,f=0,g=0,h=0,i=0,p=0;
void setup() {
  size(640, 360,P3D);
  strokeWeight(30);
  stroke(255, 160);
  
  x = width * 0.3;
  y = height * 0.5;
  translate(x,y);

}

void draw() {
  background(0);
  translate(x,y);
  stroke(255,0,0);
  strokeWeight(40);
  point(100,90);
  strokeWeight(30);
  stroke(255);
  angle1 = (mouseX/float(width) - 0.5) * -PI;//Along Z axis
  angle2 = (mouseY/float(height) - 0.5) * PI;//Along xaxis
  rotateY(angle1);
  rect(-20,-20,40,40);
  stroke(255,0,0);
  point(0,0);
  stroke(255);
  rotateZ(angle2);
  rect(10,-20,80,40);
  float dx=cos(angle1)*70*cos(angle2);
  float dy=sin(angle1)*70*cos(angle2);
  float dz=70*sin(angle2);
  translate(dx,dy-10,dz);
  stroke(255,0,0);
  point(0,0);
  stroke(255);
   if(mousePressed==true)
{angle4=(mouseX/float(width) - 0.5) * -PI;
 }
 else
 angle4=0;
  //stroke(255,0,0);
  //point(0,0);
  //stroke(255);
  //rotateZ(angle4);
 // rect(-10,-10,20,-100);
g=g+0.1; 
p=p+0.1;
}

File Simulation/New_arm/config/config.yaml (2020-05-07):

cerebroarm:
  # Publish all joint states -----------------------------------
  joint_state_controller:
    type: joint_state_controller/JointStateController
    publish_rate: 50  

  # Position Controllers ---------------------------------------
  joint1_position_controller:
    type: effort_controllers/JointPositionController
    joint: joint_1
    pid: {p: 100.0, i: 0.01, d: 10.0}
  joint2_position_controller:
    type: effort_controllers/JointPositionController
    joint: joint_2
    pid: {p: 100.0, i: 0.01, d: 10.0}
  joint3_position_controller:
    type: effort_controllers/JointPositionController
    joint: joint_3
    pid: {p: 100.0, i: 0.01, d: 10.0}
  joint4_position_controller:
    type: effort_controllers/JointPositionController
    joint: joint_4
    pid: {p: 100.0, i: 0.01, d: 10.0}
  joint5_position_controller:
    type: effort_controllers/JointPositionController
    joint: joint_5
    pid: {p: 100.0, i: 0.01, d: 10.0}
  joint6_position_controller:
    type: effort_controllers/JointPositionController
    joint: joint_6
    pid: {p: 100.0, i: 0.01, d: 10.0}
    

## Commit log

2018-09-04 cad changes
    [forearm.STL, shoulder.STL, shoulder_connector.STL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]
2018-10-01 rviz commit
    [materials.xacro, rrbot.xacro]
2018-10-10 changed CAD files
    [ardiuinosupport.stl, coverfinger1.stl, forearm.STL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]
2019-03-12 added DL code and models
    [clench_1.csv, clench_2.csv, data1.csv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]
2020-05-07 readme update
    [Armgazebo.xacro, Cerebroarm.xacro, arm-cerebro-ross - arm-1.STL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]
